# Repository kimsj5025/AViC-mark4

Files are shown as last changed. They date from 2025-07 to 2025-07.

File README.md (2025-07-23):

# AViC mark4

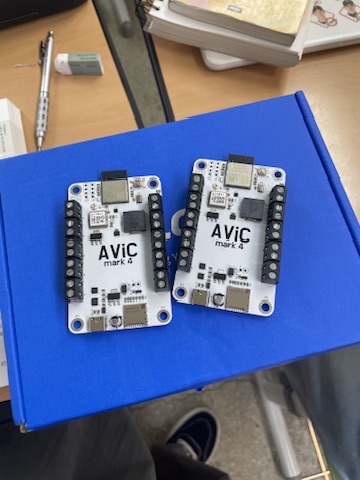
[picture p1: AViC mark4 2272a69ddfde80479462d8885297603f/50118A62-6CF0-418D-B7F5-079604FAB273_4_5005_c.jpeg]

shce
muc
pow
pcb 

이번에는 기존과는 다르게 완전 하이엔드급 보드를 제작해 보려고 하였다. 이를 위해서 TDK사의 가장 최신 센서와 20cm정확도를 갖는 기압 센서, 그리고 내장 GPS와 지자기 센서, 총 4개의 pyro까지, 필요한 모든 것들을 신용카드 사이즈의 보드 안에 통합하려고 하였다.

# 기능 테스트

- [x]  USB 업로드 테스트
- [x]  LED테스트
- [x]  I2C 스캔
- [x]  SDMMC 테스트
- [x]  wifi
- [x]  Pyro 테스트
- [x]  부저
- [x]  GNSS
- [x]  5v out
- [ ]  외부 배터리 연결시 전원 역류방지

## MPU

이번에는 풀 사이즈 Esp32 S3 wroom 1 가 아니라 esp32 s3 mini를 사용하였다.

주요 사양으로는 

- **프로세서:** Xtensa® 32비트 LX7 듀얼 코어 프로세서
- **클럭 주파수:** 최대 240 MHz
- **무선 통신:**
    - 2.4GHz Wi-Fi (802.11 b/g/n)
    - Bluetooth 5 (LE)
- **메모리:**
    - 내부 SRAM: 512KB

주요 사양은 기존의 [AViCDEsp32](https://www.notion.so/AViCDEsp32-20f2a69ddfde80878ec1d9f6c206afdb?pvs=21) 에 사용되었던 MPU와 같은 성능이다.

## 가속도계

가속도계는 TDK InvenSense사의 ICM-45686 6축 가속도 센서를 사용하였다. 이 센서는 최대 32g까지 측정할 수 있으며, 해상도는 16bit이다. 흔히 아두이노용 가속도계로 알려진 mpu6050를 만든 회사의 최신 플래그쉽 가속도 센서이다.

## 기압계

기압계는 MS5607을 사용하였다. 

이 센서의 분해능은 20cm 정도의 높이를 측정할 수 있다. 이 정도면 꽤 정확한 기압계라고 볼 수 있다.

## 자자기계

이번에는 자이로 센서의 드리프트를 보정하기 위해 LIS2MDL 3축 지자기계를 사용하였다.

## GPS

저번 보드에서는 GPS신호를 받으려면 외장 모듈을 활용해야 했지만, 이번에는 ATGM336h과 U.FL 컨넥터로 안테나만 연결해주면 GPS신호를 바로 보드에서 받을 수 있게 하였다.

또한 LED를 연결해 PPS(1초에 한번 신호를 보내는 핀)을 통해 연결 여부를 시각적으로 볼 수 있도록 해 주었다.

## Micro SD카드

저번과 같이 SDMMC를 위한 SD카드 슬롯도 배치하여 주었다.

## 모스펫 스위치

이번에는 4개의 파이로 체널로 구성되었는데. 듀얼 N타입 모스펫이 두개 들어가 있다. 각각의 배선에 따라 최대 4A의 전류를 흐르게 할 수 있다.

## 3.3V, 5V출력

저번과 같이 레귤레이터로는 AMS1117을 사용했다. 다른 점이라면 이번에는 3.3V뿐 아니라 5V도 지원이 된다는 것이다. 이는 추후 사용할 카메라인 Runcam Split 4 4k가 최소 5V 입력을 지원하기에, 이를 보드 내에서 처리하기 위함이다.

## LED 인디케이터

저번 보드에서의 문제점이 이게 작동 중인지 아닌지 관계 없이 전원이 들어오면 LED가 계속 켜져있는다는 것이였는데, 이를 해결하기 위해 MPU에서 직접 이를 조정하게 해 이 문제를 해결했다.

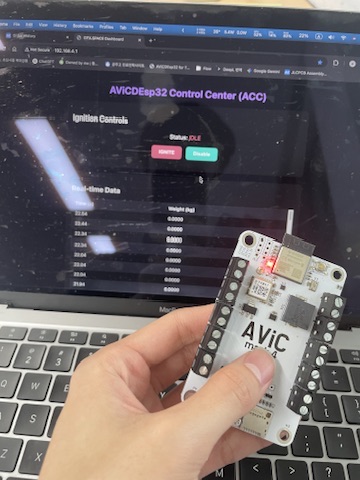
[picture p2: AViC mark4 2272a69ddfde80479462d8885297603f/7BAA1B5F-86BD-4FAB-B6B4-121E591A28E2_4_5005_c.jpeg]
웹에서 센서 데이터를 읽어올 때 마다 LED가 깜빡이게 만든 모습


웹에서 센서 데이터를 읽어올 때 마다 LED가 깜빡이게 만든 모습

## 부저

이 는 원래 에이비오닉스로 활용될 계획도 갖고 있어서, 로켓 내부에 있을 때에 청각적으로 작동중임을 알 수 있도록 부저를 달아서 알 수 있게 하였다.

또한 부팅시에 부팅음을 넣어서 시리얼 모니터를 보지 않아도 정상적으로 리셋이 되었는지 알 수 있도록 하였다.

## USB-C

ESP32 s3는 풀 스피드 USB2.0를 지원하고 내장 CDC가 있기 때문에 D- D+핀만 정상적으로 연결해 준다면 usb를 이용하여 코딩과 시리얼 모니터(UART0)를 볼 수 있다. 또한 USB에서 나오는 5V전원을 통해 보드 전체의 전원이 들어올 수 있도록 해 주었다. 이를 통해 기존 코드 업로드 방식에서 엄청난 혁신을 이루었는데, 코드를 업로드 할 때마다 리셋 버튼을 누르는 수고와 항상 USB TTL컨버터를 찾아야 하는 번거로움에서 해방되었다. (그래서 USB TTL컨버터를 잃어버렸다;)

또한 이 USB-C에 대한 글을 하나 작성하였다. 

https://kimsj5025.tistory.com/entry/Esp32-S3-USB-OTG-%EC%8B%9C%EB%A6%AC%EC%96%BC-%EB%AA%A8%EB%8B%88%ED%84%B0%EA%B0%80-%EC%95%88%EB%82%98%EC%98%AC%EB%95%8C-%ED%95%B4%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

## 더 많은 GPIO

PWM용, UART 통신(+ RX TX -)을 위한 헤더핀 총 8개 그리고 3.3,5V 각각 두개, 4개의 파이로 체널, 9개의 GPIO, 3개의 GND 총 20개의 터미널 블럭을 이용한 단자를 만들어 주었다. 또한 각가그이 M4 나사 규격의 마운트홀도 모두 GND에 연결해 주어 총 7개의 GND단자가 있게 되었다.

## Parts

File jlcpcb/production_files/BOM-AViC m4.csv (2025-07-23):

Comment | Designator | Footprint | LCSC | Quantity
27n | L1 | L_0603_1608Metric | C12100 | 1
SI7232DN-T1-GE3 | Q1,Q2 | mosfet_custom | C144854 | 2
0.1uF | C14,C15,C17,C3,C8 | C_0603_1608Metric | C14663 | 5
1uF | C18 | C_0603_1608Metric | C15849 | 1
USB_C_Receptacle_USB2.0_16P | J5 | USB_C_Receptacle_HCTL_HC-TYPE-C-16P-01A | C165948 | 1
10uF | C9 | C_0603_1608Metric | C19702 | 1
220nF | C6 | C_0603_1608Metric | C21120 | 1
1KR | R10 | R_0603_1608Metric | C21190 | 1
RED | D1,D4 | LED_0603_1608Metric_Pad1.05x0.95mm_HandSolder | C2286 | 2
330 | R19 | R_0603_1608Metric | C23138 | 1
4.7k | R6,R7,R8,R9 | R_0603_1608Metric | C23162 | 4
5k1 | R12,R13 | R_0603_1608Metric | C23186 | 2
100k | R11 | R_0603_1608Metric | C25803 | 1
10k | R1,R14,R16,R17,R18,R2,R3,R4,R5 | R_0603_1608Metric | C25804 | 9
ESP32-S3-MINI-1 | U8 | ESP32-S2-MINI-1 | C2913206 | 1
Flash Mode | SW1 | SW_SPST_PTS645 | C318884 | 1
47uF | C10 | CP_Elec_5x5.4 | C3337 | 1
Power ternimal LEFT | J10,J11,J13,J14,J15,J16,J3,J6,J7,J9 | TerminalBlock_MaiXu_MX126-5.0-02P_1x02_P5.00mm | C430623 | 10
Conn_Coaxial | J4 | U.FL_Molex_MCRF_73412-0110_Vertical | C5137195 | 1
Micro_SD_Card_Det_Hirose_DM3AT | J1 | microSD_HC_Molex_104031-0811 | C585350 | 1
Buzzer | BZ1 | Buzzer_Mallory_AST1240MLQ | C7421651 | 1
~ | U4 | ATGM336h | C90770 | 1
10uF | C1,C16,C2,C4,C5,C7 | C_0603_1608Metric | C96446 | 6
MS5607-02BA | U3 | LGA-8_3x5mm_P1.25mm | C97627 | 1
PWM | J12 | PinHeader_1x04_P2.54mm_Vertical |  | 1
Lora | J2 | PinHeader_1x04_P2.54mm_Vertical |  | 1
SS14 | D2 | D_SMA |  | 1
USBLC6-2SC6 | U5 | SOT-23-6 |  | 1
LIS2MDL | U2 | LGA-12_2x2mm_P0.5mm |  | 1
AMS1117-3.3 | U6 | SOT-223-3_TabPin2 |  | 1
ICM-45686 | U1 | LGA-14_3x2.5mm_P0.5mm_LayoutBorder3x4y |  | 1
AMS1117-5.0 | U7 | SOT-223-3_TabPin2 |  | 1
Batt | J8 | PinHeader_1x02_P2.54mm_Vertical |  | 1
DMG2302U | Q3 | SOT-23 |  | 1

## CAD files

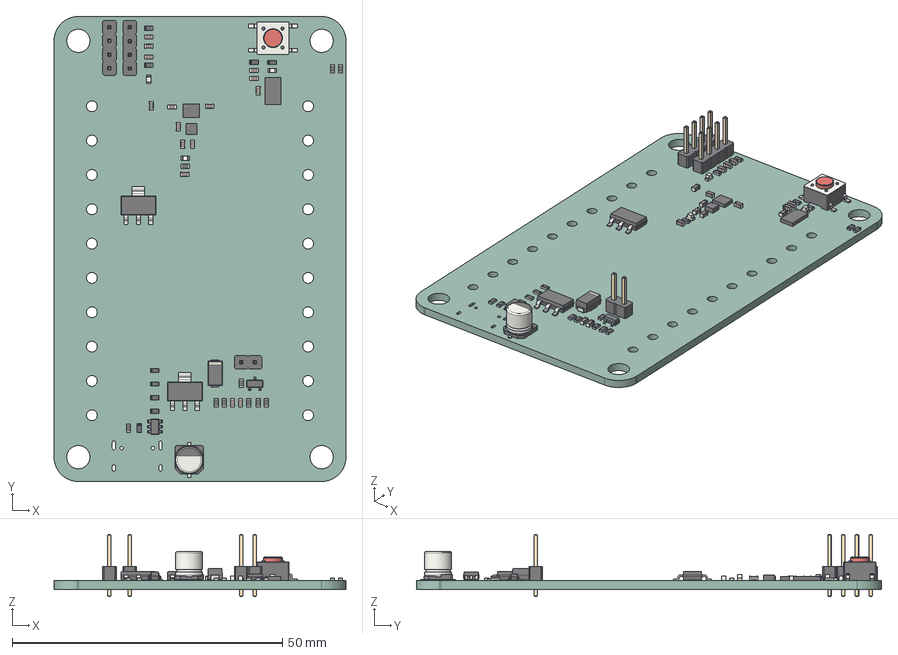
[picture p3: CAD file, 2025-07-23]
AViC m4.step
54.0 x 86.0 x 11.5 mm
PinHeader_1x04_P254mm_Vertical x 2
D_SMA
R_0603_1608Metric x 19
C_0603_1608Metric x 14
L_0603_1608Metric
LED_0603_1608Metric x 3
SW_SPST_PTS645
SOT_23_6
LGA_12_2x2mm_P05mm
SOT_223 x 2
LGA_14_3x25mm_P05mm_LayoutBorder3x4y
CP_Elec_5x54
PinHeader_1x02_P254mm_Vertical
LGA_8_3x5mm_P125mm
SOT_23
AViC m4_PCB

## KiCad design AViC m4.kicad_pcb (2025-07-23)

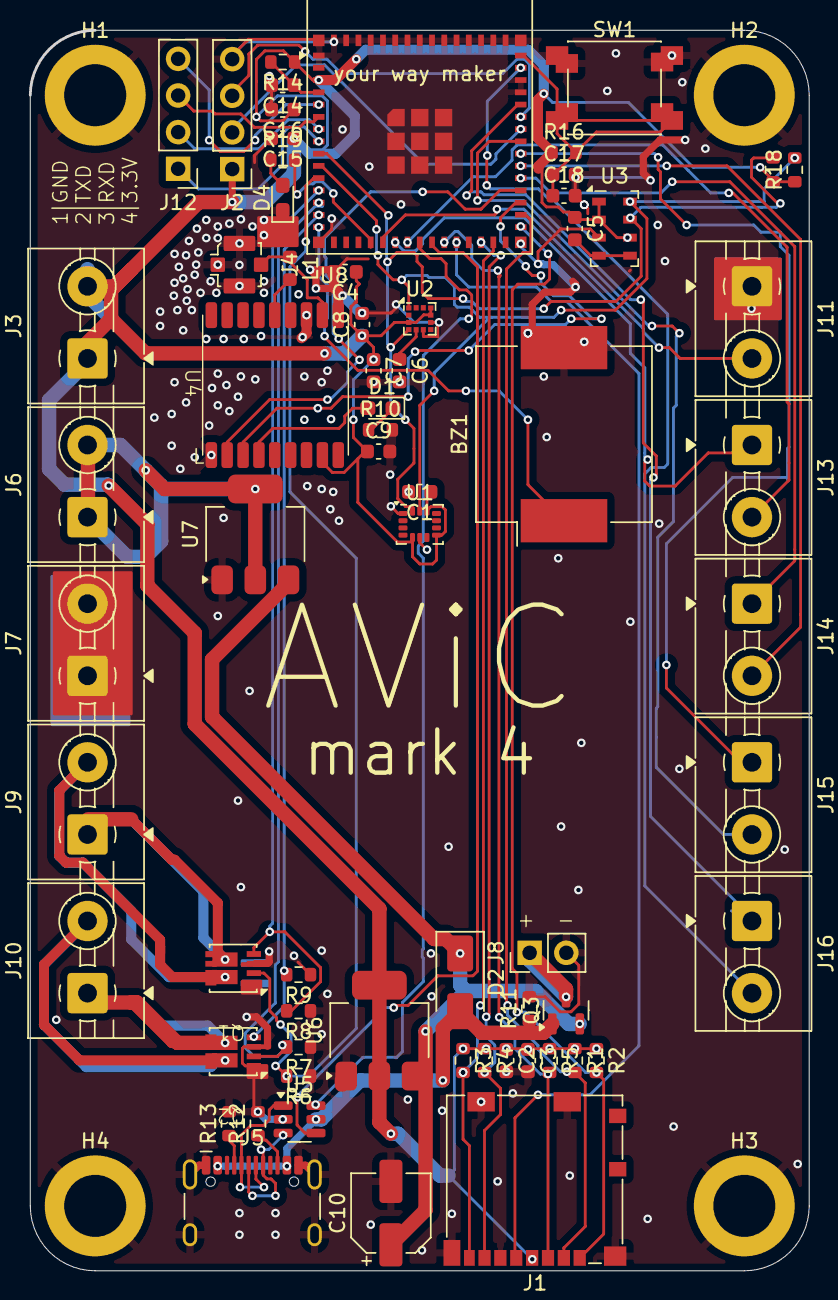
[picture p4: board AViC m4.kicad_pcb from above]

Board: 2 copper layers, 54.0 x 86.0 mm, 70 parts (0 on the bottom side), 56 nets.

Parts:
BZ1: Buzzer; Buzzer_Mallory_AST1240MLQ
C1, C2, C4, C5, C7, C9, C16: 10uF; C_0603_1608Metric
C3, C8, C14, C15, C17: 0.1uF; C_0603_1608Metric
C6: 220nF; C_0603_1608Metric
C10: 47uF; CP_Elec_5x5.4
C18: 1uF; C_0603_1608Metric
D1: RED; LED_0603_1608Metric_Pad1.05x0.95mm_HandSolder
D2: SS14; D_SMA
D4: LED; LED_0603_1608Metric_Pad1.05x0.95mm_HandSolder
H1, H2, H3, H4: m4; MountingHole_4.3mm_M4_ISO14580_Pad
J1: Micro_SD_Card_Det_Hirose_DM3AT; microSD_HC_Molex_104031-0811
J2: Lora; PinHeader_1x04_P2.54mm_Vertical
J3, J6, J7, J9, J10: Power ternimal LEFT; TerminalBlock_MaiXu_MX126-5.0-02P_1x02_P5.00mm
J4: Conn_Coaxial; U.FL_Molex_MCRF_73412-0110_Vertical
J5: USB_C_Receptacle_USB2.0_16P; USB_C_Receptacle_HCTL_HC-TYPE-C-16P-01A
J8: Batt; PinHeader_1x02_P2.54mm_Vertical
J11, J13, J14, J15, J16: GPIOs; TerminalBlock_MaiXu_MX126-5.0-02P_1x02_P5.00mm
J12: PWM; PinHeader_1x04_P2.54mm_Vertical
L1: 27n; L_0603_1608Metric
Q1, Q2: SI7232DN-T1-GE3; mosfet_custom
Q3: DMG2302U; SOT-23
R1, R2, R3, R4, R5, R14, R16, R17, R18: 10k; R_0603_1608Metric
R6, R7, R8, R9: 4.7k; R_0603_1608Metric
R10: 1KR; R_0603_1608Metric
R11: 100k; R_0603_1608Metric
R12, R13: 5k1; R_0603_1608Metric
R19: 330; R_0603_1608Metric
SW1: Flash Mode; SW_SPST_PTS645
U1: ICM-45686; LGA-14_3x2.5mm_P0.5mm_LayoutBorder3x4y
U2: LIS2MDL; LGA-12_2x2mm_P0.5mm
U3: MS5607-02BA; LGA-8_3x5mm_P1.25mm
U4: ATGM336h
U5: USBLC6-2SC6; SOT-23-6
U6: AMS1117-3.3; SOT-223-3_TabPin2
U7: AMS1117-5.0; SOT-223-3_TabPin2
U8: ESP32-S3-MINI-1; ESP32-S2-MINI-1

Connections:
+3.3V: C1.1, C2.1, C3.1, C4.1, C5.1, C7.1, C8.1, C9.1, C15.1, C16.1, J1.4 (VDD), J2.1, J3.1, J3.2, R1.1, R2.1, R3.1, R4.1, R5.1, R14.1, R16.1, R17.1, R18.1, U1.5 (VDDIO), U1.8 (VDD), U1.12 (AP_CS), U2.3 (~CS), U2.9 (Vdd), U2.10 (Vdd_IO), U3.1 (VDD), U3.2 (PS), U3.6 (SDO), U4.8 (VCC), U6.2 (VO), U8.3 (3V3)
+5V: J6.1, J6.2, U7.2 (VO)
+BATT: J8.1, Q3.3 (D)
/MCU/FLASH: C14.1, R14.2, U8.4 (IO0)
/MCU/LED: R19.2, U8.19 (IO15)
/MCU/PWM 1: J12.4, U8.5 (IO1)
/MCU/PWM 2: J12.3, U8.6 (IO2)
/MCU/PWM 3: J12.2, U8.7 (IO3)
/MCU/PWM 4: J12.1, U8.8 (IO4)
/MCU/RESET: C17.1, C18.1, R16.2, SW1.2, U8.45 (EN)
/MCU/UART0_RXD: J2.3, U8.40 (RXD0)
/MCU/UART0_TXD: J2.2, U8.39 (TXD0)
/functions/1PPS: D1.2 (A), U4.4 (1PPS)
/functions/GPS_ANT: J4.1 (In), L1.1, U4.11 (RF_IN)
/functions/SW1: J9.1, Q1.7
/functions/SW2: J9.2, Q1.6
/functions/SW3: J10.1, Q2.7
/functions/SW4: J10.2, Q2.6
/functions/VCC_RF: L1.2, U4.14 (VCC_RF)
BUZZER: BZ1.1 (+), U8.15 (IO11)
CLK: J1.5 (CLK), U8.26 (IO26)
CMD: J1.3 (CMD), R5.2, U8.25 (IO21)
D+: U5.4 (I/O2), U8.24 (USB_D+)
D-: U5.6 (I/O1), U8.23 (USB_D-)
DAT0: J1.7 (DAT0), R4.2, U8.28 (IO33)
DAT1: J1.8 (DAT1), R3.2, U8.29 (IO34)
DAT2: J1.1 (DAT2), R2.2, U8.31 (IO35)
DAT3: J1.2 (DAT3/CD), R1.2, U8.32 (IO36)
GND: BZ1.2 (-), C1.2, C2.2, C3.2, C4.2, C6.2, C7.2, C8.2, C9.2, C10.2, C14.2, C15.2, C16.2, C17.2, C18.2, D4.1 (K), H1.1, H2.1, H3.1, H4.1, J1.6 (VSS), J1.11 (SHIELD), J2.4, J4.2 (Ext), J5.A1 (GND), J5.A12 (GND), J5.B1 (GND), J5.B12 (GND), J5.S1 (SHIELD), J7.1, J7.2, J8.2, J11.1, Q1.1, Q1.3, Q2.1, Q2.3, R6.1, R7.1, R8.1, R9.1, R10.2, R11.2, R12.2, R13.2, SW1.1, U1.1 (AP_SDO/AP_AD0), U1.6 (GND), U2.6 (GND), U2.8 (GND), U3.3 (GND), U4.1 (GND), U4.10 (GND), U4.12 (GND), U5.2 (GND), U6.1 (GND), U7.1 (GND), U8.1 (GND), U8.2 (GND), U8.42 (GND), U8.43 (GND), U8.46 (GND), U8.47 (GND), U8.48 (GND), U8.49 (GND), U8.50 (GND), U8.51 (GND), U8.52 (GND), U8.53 (GND), U8.54 (GND), U8.55 (GND), U8.56 (GND), U8.57 (GND), U8.58 (GND), U8.59 (GND), U8.60 (GND), U8.61 (GND), U8.62 (GND), U8.63 (GND), U8.64 (GND), U8.65 (GND)
GPIO16: J11.2, U8.20 (IO16)
GPIO17: J13.1, U8.21 (IO17)
GPIO18: J13.2, U8.22 (IO18)
GPS RX: U4.3 (RD), U8.33 (IO37)
GPS TX: U4.2 (TX), U8.34 (IO38)
unnamed: C5.2, U3.4 (CSB), U3.5 (CSB)
unnamed: D1.1 (K), R10.1
unnamed: C10.1, D2.1 (K), Q3.2 (S), U6.3 (VI), U7.3 (VI)
unnamed: D4.2 (A), R19.1
unnamed: J5.A5 (CC1), R13.1
unnamed: J5.B5 (CC2), R12.1
unnamed: J5.A6 (D+), J5.B6 (D+), U5.3 (I/O2)
unnamed: J5.A7 (D-), J5.B7 (D-), U5.1 (I/O1)
unnamed: J14.1, U8.35 (IO39)
unnamed: J14.2, U8.36 (IO40)
unnamed: J15.1, U8.37 (IO41)
unnamed: J15.2, U8.38 (IO42)
unnamed: J16.1, U8.41 (IO45)
unnamed: J16.2, U8.44 (IO46)
unnamed: C6.1, U2.5 (C1)
SCL: R18.2, U1.13 (AP_SCL/AP_SCLK), U2.1 (SCL/SPC), U3.8 (SCLK), U8.10 (IO6)
SDA: R17.2, U1.14 (AP_SDA/AP_SDIO/AP_SDI), U2.4 (SDA/SDI/SDO), U3.7 (SDI/SDA), U8.9 (IO5)
SW1 control: Q1.2, R6.2, U8.11 (IO7)
SW2 control: Q1.4, R8.2, U8.12 (IO8)
SW3 control: Q2.2, R7.2, U8.13 (IO9)
SW4 control: Q2.4, R9.2, U8.14 (IO10)
VBUS: D2.2 (A), J5.A4 (VBUS), J5.A9 (VBUS), J5.B4 (VBUS), J5.B9 (VBUS), Q3.1 (G), R11.1, U5.5 (VBUS)

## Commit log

2025-07-23 README.MD (notion ver)
    노션에 써 놓은 것을 Export해서 올려봅니다.
    사진도 같이 올라갈진 모르겠음
2025-07-23 to-do list 하나 삭제
